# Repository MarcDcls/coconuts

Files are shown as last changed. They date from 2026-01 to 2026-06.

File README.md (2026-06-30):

# CocoNuts Project







The **CocoNuts project** is an open-source humanoid robotics research platform. Its primary design philosophy is the **minimization of leg inertia** by concentrating mass near the root of the limbs, utilizing a combination of timing belts and parallel linkage mechanisms. This repository contains the hardware design of the CocoNuts humanoid platform and the software to operate it with a CANalyst-II interface.

The CAD of the CocoNuts platform is open-source and available under the CERN-OHL-S-2.0 license 
[here](https://cad.onshape.com/documents/326c7618f048bbd5c9f71f42/v/8ddbb93e8d16fabe401f72ed/e/6f8aa33372eceae3daea128b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). The motors used in the robot are RMD-X6 QDD actuators and TD30-40 and TD40-52 harmonic drive actuators.

The software provided is distributed under the Apache-2.0 license and is implemented in Python, which is not adapted for real-time control, but allows to easily set up and test the servomotors and the mechanical design. 

## Mechanical Design

The CocoNuts humanoid platform is designed to minimize leg inertia by relocating the mass of the actuators closer to the body. This is achieved using timing belts at the output of the RMD-X6 motors 
to place the knee and ankle pitch motors near the hip joint:

<p align="center">
  
  
<p\>
  
The transmission of ankle pitch motion is then achieved using a four-bar parallel linkage mechanism:

<p align="center">
  
  
<p\>
  
## Simplified One Leg Benchmark

The prototype of a one leg benchmark of the CocoNuts platform was built to evaluate the performance of the design concept. The CAD of this prototype is available [here](https://cad.onshape.com/documents/326c7618f048bbd5c9f71f42/v/8ddbb93e8d16fabe401f72ed/e/362dba3e9b9b20be3e7fcf95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). Example trajectories were run on the leg to assess its capabilities in three configurations: ankle only actuation, knee only actuation, and both knee and ankle actuation.

<p align="center">
  ankle
  ankle_gif
<p\>

<p align="center">
  knee
  knee_gif
<p\>

<p align="center">
  both
  both_gif
<p\>

The experiments provided critical insights into the platform's design:
- **Actuator Mismatch**: The RMD-X6 motors proved to be oversized for the current scale of the leg. Their high torque capability is offset by their weight, resulting in an unfavorable power-to-weight ratio for this specific frame. This suggests that the design would be more efficient either with a larger structural scale or with lighter, more compact actuators.
- **Mechanical Complexity**: The timing belt and parallel linkage system, while successful in shifting mass towards the body, introduced significant compliance and mechanical play. This complexity led to challenges in achieving precise control.

These findings indicate that a major architectural pivot is required to better align the actuation power with the mechanical structure. As a result, the project is currently on hold and I am maintaining this repository as an open-access technical reference for the robotics community.

# Control Software 

This part of the repository contains the software to operate the RMD-X6 servomotors using a CANalyst-II interface. The software is implemented in Python and allows to set up and test the servomotors.

## Install

To install the repository, you need the uv package manager. 
If you don't have it yet, you can install it by following the instructions [here](https://docs.astral.sh/uv/getting-started/installation/#installation-methods).

Then, clone this repository and run the following command in your terminal:
```
uv sync
```

To use the CANalyst-II device, you need to add a rule to grant USB permissions. To do so, copy the 99-canalyst.rules file provided to 
the `/etc/udev/rules.d/` directory:
```
sudo cp 99-canalyst.rules /etc/udev/rules.d/.
```

## List of motor commands

Several scripts are provided to set up the RMD-X6 servomotors. The available commands are:
- `./set_id.sh <new_id>`: Set the ID of the connected servomotor to `<new_id>`.
- `./ping.sh <ids>`: Ping the list of `<ids>` to check if the servomotors are connected.
- `./set_zeros.sh`: Set the current position of all servomotors as their zero position in their ROM.
- `./stop.sh`: Stop and release all servomotors.
- `./state.sh <ids>`: Display the state (temperature, position, velocity, current, last timestep of reading) of the servomotors in the list of `<ids>`.
- `./set_filter.sh <bool> <ids>`: Set the CAN filter to enable (`<bool>` = 1) or disable (`<bool>` = 0) filtering for the list of `<ids>`. 
- `./set_acceleration.sh <acceleration> <ids>`: Set the maximum acceleration/deceleration for the velocity and position control modes of the servomotors in the list of `<ids>` to `<acceleration>`. Setting `<acceleration>` to 0 disables the acceleration limit and the acceleration follow the default profile of the servomotor.
- `./set_pid.sh <id> <kp> <ki>`: Set the Kp and Ki gains of the servomotor `<id>` to `<kp>` and `<ki>`.
- `./read_rom.sh <ids>`: Display the ROM parameters (acc/dec of the control modes, PID gains) of the servomotors in the list of `<ids>`.

The commands are implemented in the `software/rmd_motor.py` file, which can also be imported as a module in your own Python scripts to write custom motor scripts.

## One leg benchmark

The one leg benchmark can be controlled using the `benchmark.sh` script. The script runs a series of trajectories to test the performance of the leg design. By default, the benchmark runs these trajectories in a meshcat visualizer to verify the motion of the leg before running it physically.

Prior to running the benchmark on the real hardware, make sure to set up the motors by:
- Setting the knee motor ID to 1 and the ankle motor ID to 2 using the `set_id.sh` script.
- Deactivating the CAN filters for both motors using the command `./set_filter.sh 0 1 2`.
- Setting the zero positions of both motors using the command `./set_zeros.sh` while the leg is extended with the foot horizontal. You can verify the zero positions by running the command `./state.sh 1 2` and checking that both motors read a position of 0.
- Setting the acceleration limits of both motors to 0 using the command `./set_acceleration.sh 0 1 2`.

Once the setup is complete, you can run the benchmark using the command:
```
./benchmark.sh <option>
```

where `<option>` can be:
- `--plot`: Plot the motor trajectories instead of running the visualization.
- `--send`: Run the benchmark on the real hardware instead of the visualization.
- `--duration <seconds>`: Set the duration of the trajectory to `<seconds>`.
- `--ankle_only`: Run a sinusoidal trajectory on the ankle motor only.
- `--knee_only`: Run a sinusoidal trajectory on the knee motor only, with the ankle fixed.
- `--zero`: Run a zero position trajectory.

By default the trajectory consists of a sinusoidal motion of both the knee and ankle motors with a duration of 4 * pi seconds.

# Citation

To cite this repository in your publications:
```bibtex
@software{mduclusaud-coconuts,
    author = {Duclusaud, Marc},
    doi = {10.5281/zenodo.18470949},
    month = feb,
    title = {{CocoNuts: An open-source humanoid robotics platform minimizing leg inertia}},
    url = {https://github.com/MarcDcls/coconuts},
    howpublished = "\url{https://github.com/MarcDcls/coconuts}",
    version = {1.0.0},
    year = {2026}
}
```

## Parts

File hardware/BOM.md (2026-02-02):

# Bill of Materials

- 4x RMD X6 1:6 
- 4x TD 30-40
- 4x TD 40-52

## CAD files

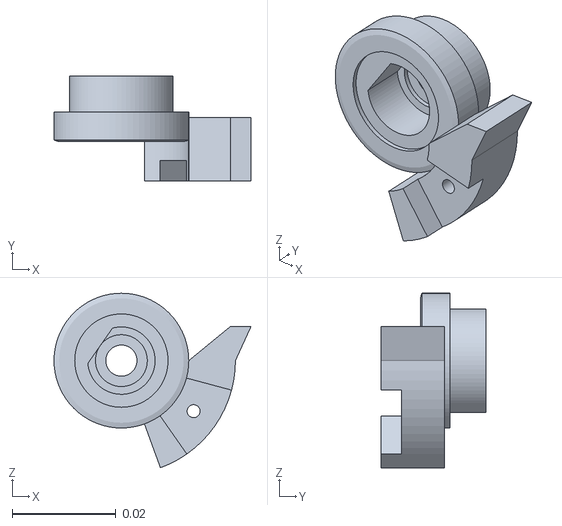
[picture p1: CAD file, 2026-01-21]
hardware/benchmark/assets/benchmark_outer_knee.stl
0.038 x 0.0203 x 0.0337

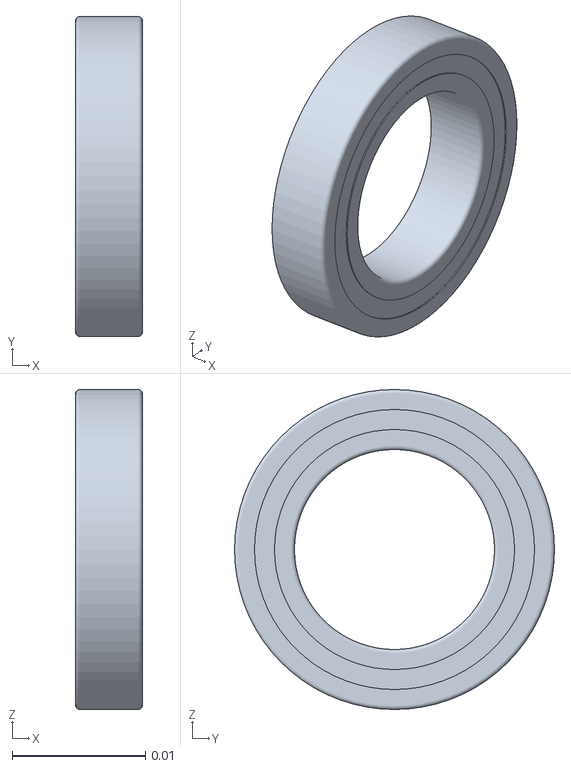
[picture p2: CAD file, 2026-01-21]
hardware/benchmark/assets/bearing_6802_2rs.stl
0.005 x 0.024 x 0.024

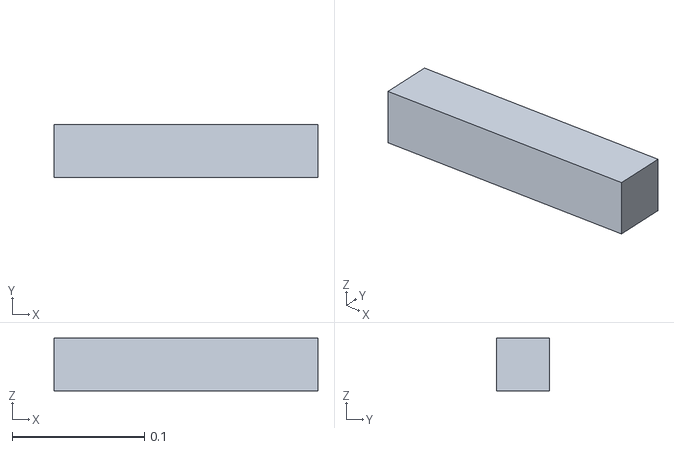
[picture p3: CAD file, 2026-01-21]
hardware/benchmark/assets/aluminum_profile.stl
0.2 x 0.04 x 0.04

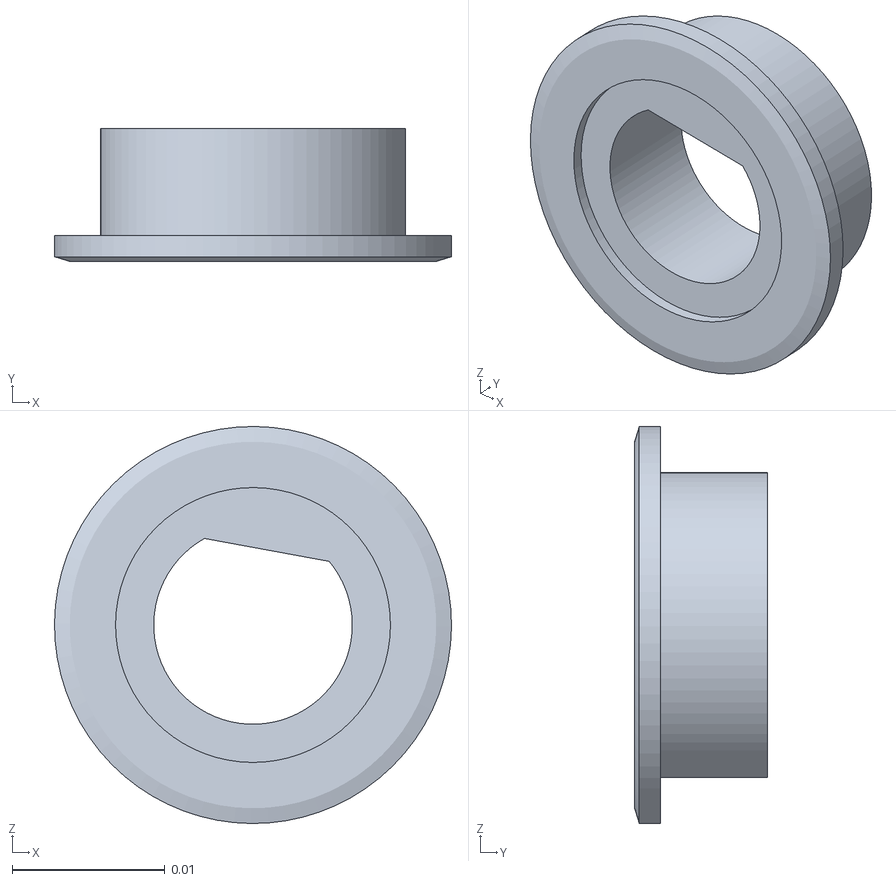
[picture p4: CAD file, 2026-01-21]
hardware/benchmark/assets/outer_crank.stl
0.026 x 0.0087 x 0.026

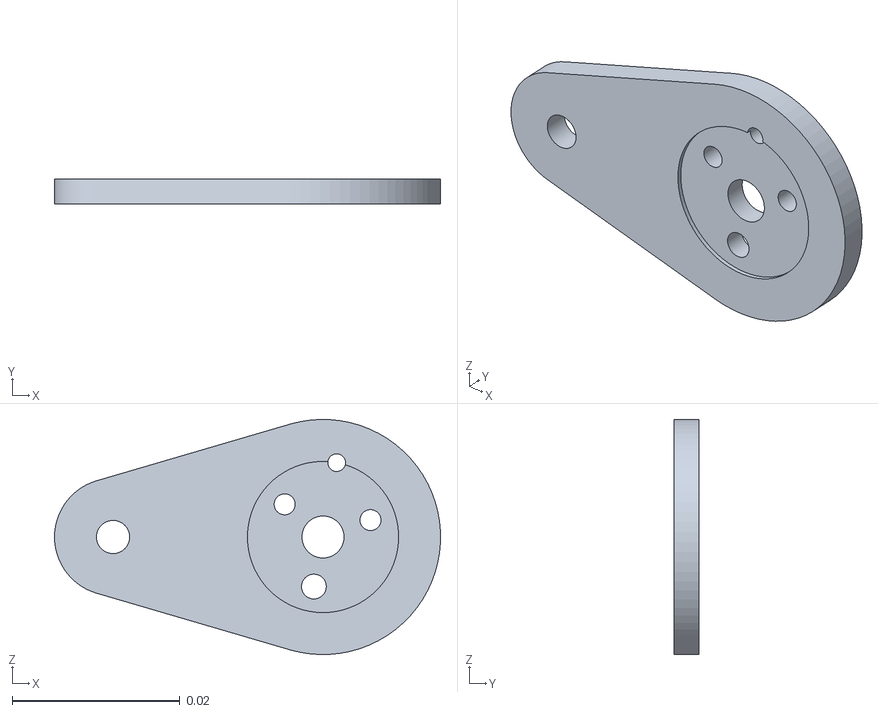
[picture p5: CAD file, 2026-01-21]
hardware/benchmark/assets/outer_crank_alu_mirror.stl
0.046 x 0.003 x 0.028

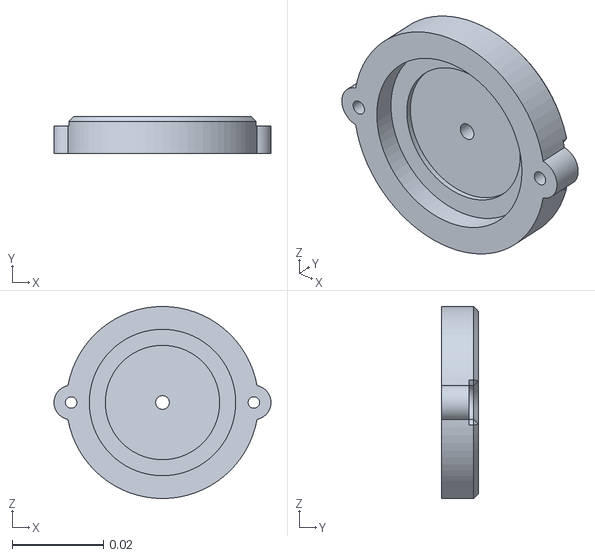
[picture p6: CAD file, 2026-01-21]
hardware/benchmark/assets/bearing_cover_1.stl
0.0474 x 0.008 x 0.042

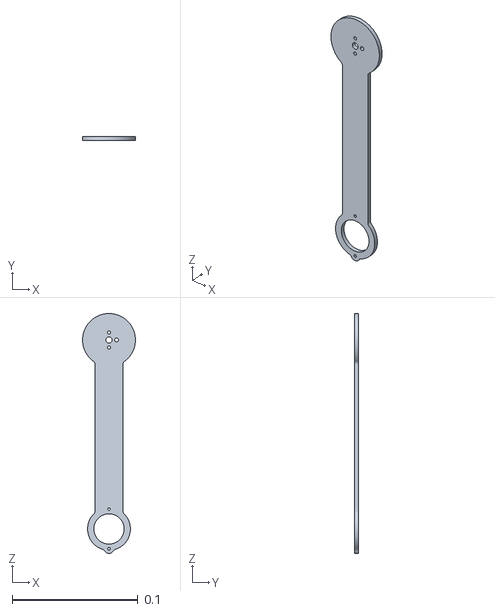
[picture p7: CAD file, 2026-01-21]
hardware/benchmark/assets/inner_tibia.stl
0.042 x 0.003 x 0.19

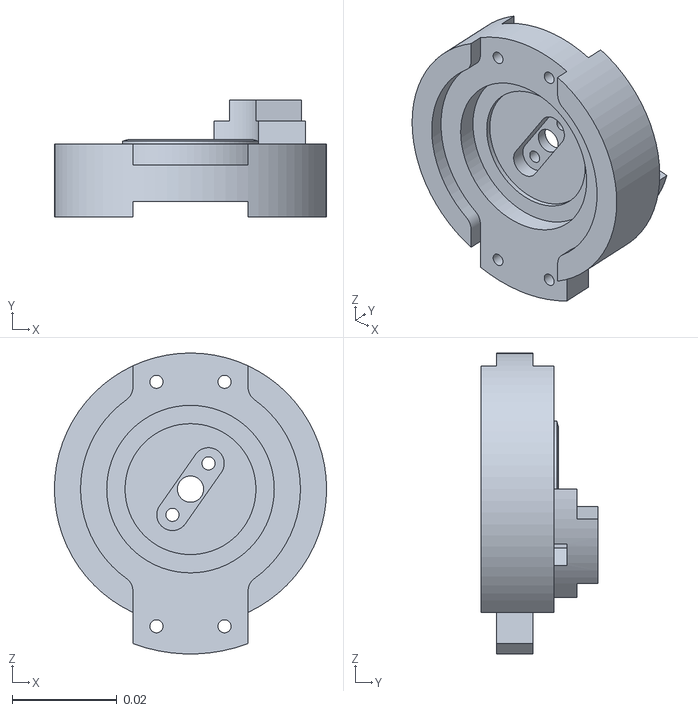
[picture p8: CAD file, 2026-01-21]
hardware/benchmark/assets/outer_knee_2.stl
0.052 x 0.0224 x 0.0575

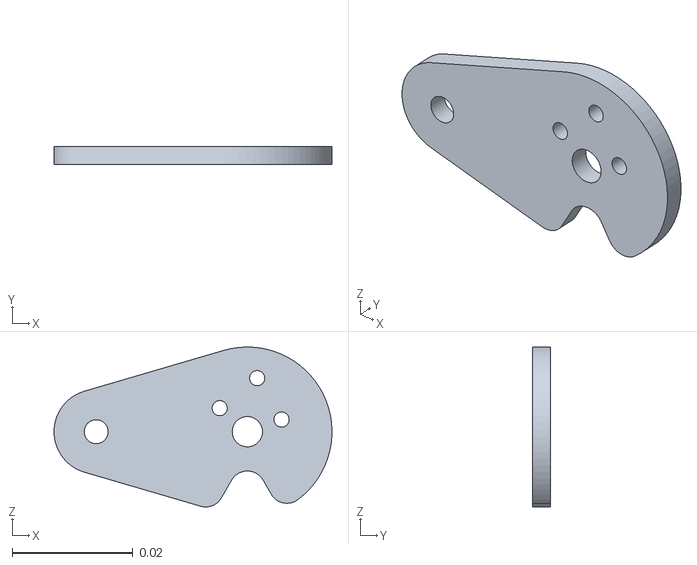
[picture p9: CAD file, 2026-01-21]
hardware/benchmark/assets/inner_crank_alu.stl
0.046 x 0.003 x 0.0264

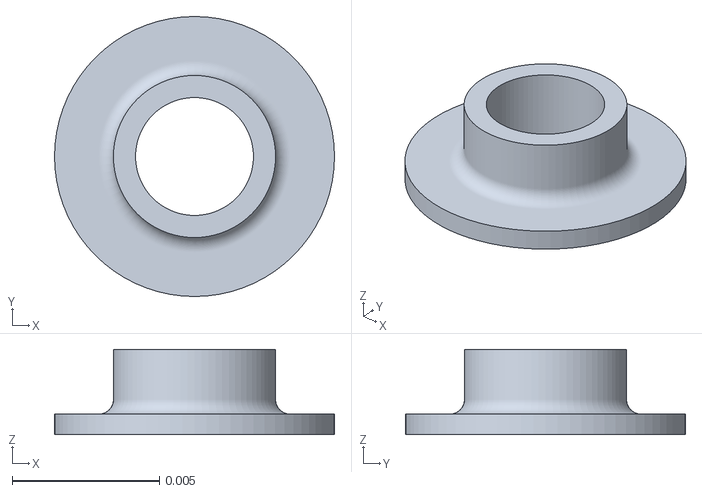
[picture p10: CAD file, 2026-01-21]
hardware/benchmark/assets/p210fm_plain_bearing.stl
0.0095 x 0.0095 x 0.0029

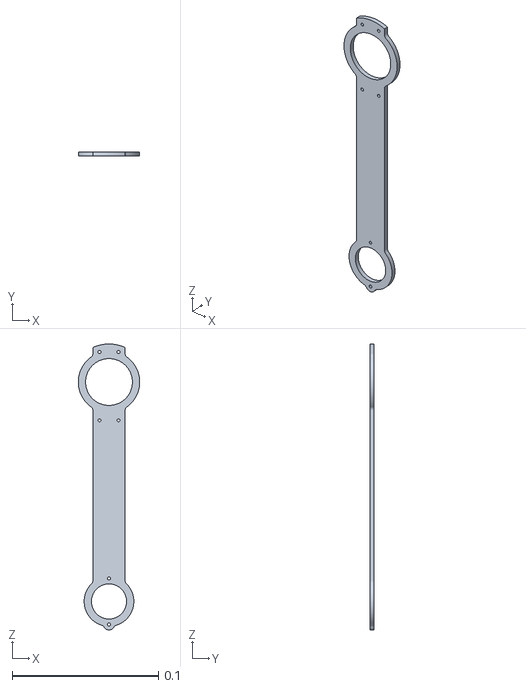
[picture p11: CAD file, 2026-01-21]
hardware/benchmark/assets/outer_tibia.stl
0.042 x 0.003 x 0.195

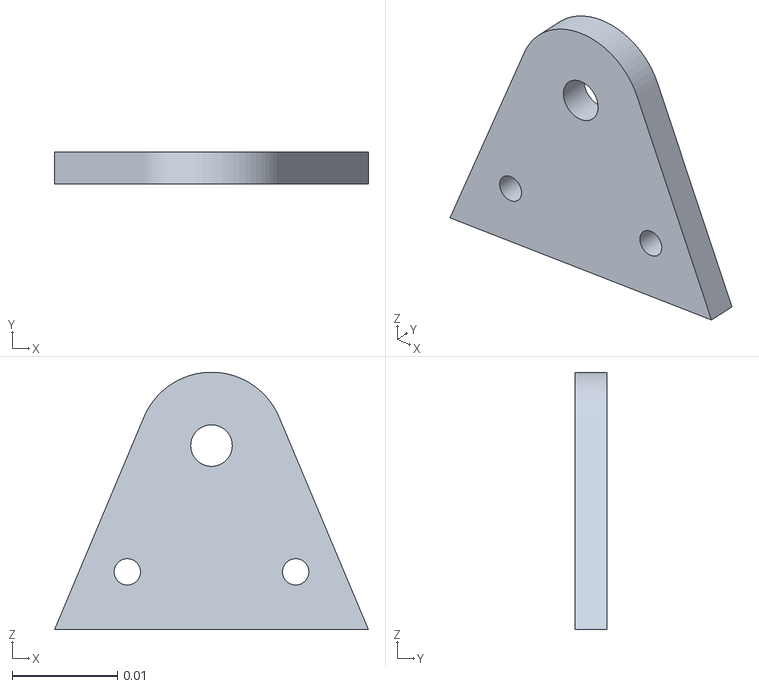
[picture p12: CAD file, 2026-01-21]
hardware/benchmark/assets/ankle_alu.stl
0.0298 x 0.003 x 0.0245

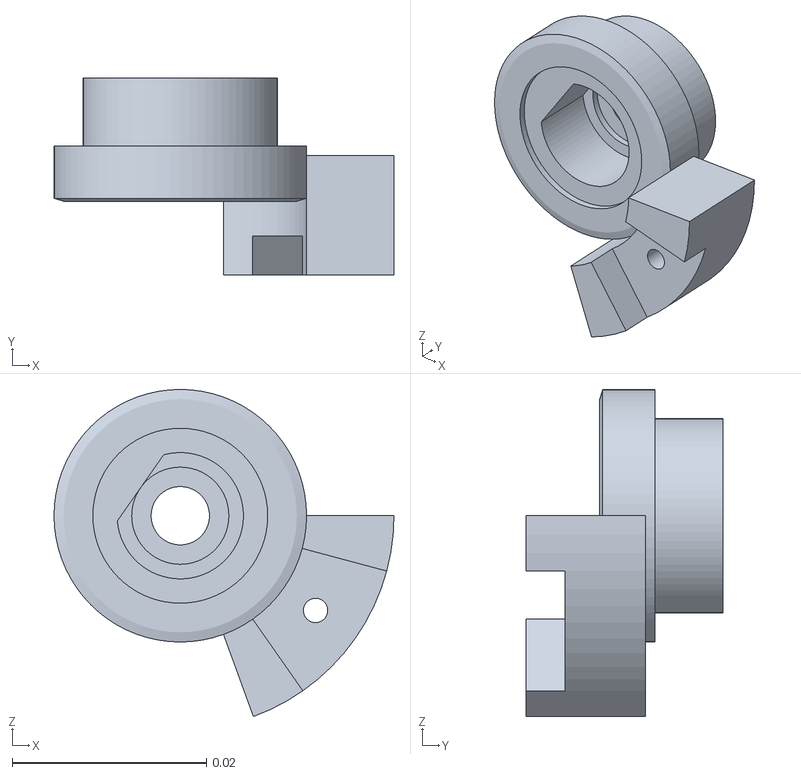
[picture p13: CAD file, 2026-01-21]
hardware/benchmark/assets/outer_knee_1.stl
0.035 x 0.0203 x 0.0337

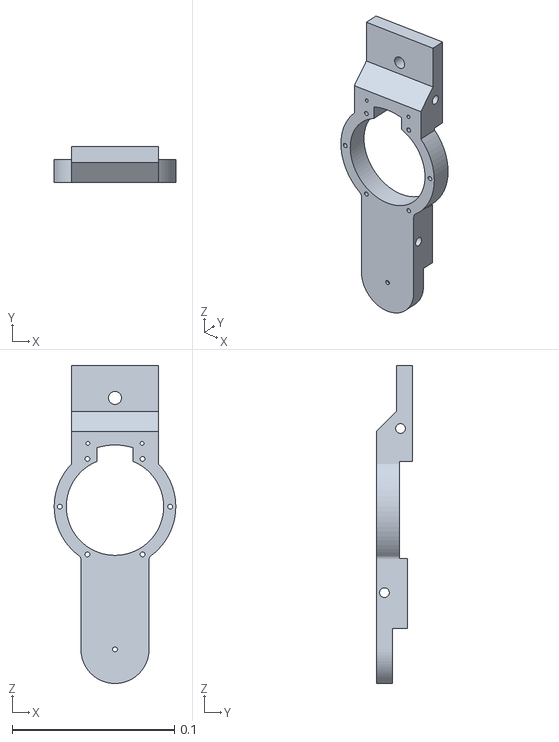
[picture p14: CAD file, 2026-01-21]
hardware/benchmark/assets/benchmark_inner_femur.stl
0.075 x 0.0224 x 0.196

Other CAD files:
hardware/benchmark/assets/benchmark_back_cover.stl
hardware/benchmark/assets/middle_crank.stl
hardware/benchmark/assets/benchmark_outer_hip.stl
hardware/benchmark/assets/inner_crank_mirror.stl
hardware/benchmark/assets/ankle_bearing_cover.stl
hardware/benchmark/assets/ankle_mirror.stl
hardware/benchmark/assets/ankle_shaft.stl
hardware/benchmark/assets/bearing_6804_2rs.stl
hardware/benchmark/assets/benchmark_foot.stl
hardware/benchmark/assets/benchmark_front_cover.stl
hardware/benchmark/assets/benchmark_outer_femur.stl
hardware/benchmark/assets/din_6325_3mm__configuration__12.stl
hardware/benchmark/assets/din_6325_3mm__configuration__6.stl
hardware/benchmark/assets/din_6325_4mm__configuration__14.stl
hardware/benchmark/assets/din_6325_4mm__configuration__20.stl
hardware/benchmark/assets/inner_knee.stl
hardware/benchmark/assets/knee_pulley.stl
hardware/benchmark/assets/knee_pulley_2.stl
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

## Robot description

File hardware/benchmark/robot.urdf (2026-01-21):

<?xml version="1.0" ?>
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
<robot name="benchmark">
  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
  <link name="aluminum_profile">
    <inertial>
      <origin xyz="0 0 0" rpy="0 0 0"/>
      <mass value="0"/>
      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
    </inertial>
    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
  </link>
  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
  <link name="motor_pulley">
    <inertial>
      <origin xyz="-6.05622e-16 4.59528e-05 -0.010399" rpy="0 0 0"/>
      <mass value="0.0695532"/>
      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
    </inertial>
    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
  </link>
  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
  <joint name="knee_motor" type="revolute">
    <origin xyz="-0.000132957 0 0.42" rpy="1.5708 5.23711e-65 3.14159"/>
    <parent link="aluminum_profile"/>
    <child link="motor_pulley"/>
    <axis xyz="0 0 1"/>
    <limit effort="10" velocity="10" lower="-3.141592653589793" upper="3.141592653589793"/>
  </joint>
  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
  <link name="inner_knee">
    <inertial>
      <origin xyz="0.000201294 -0.0560108 -0.0375295" rpy="0 0 0"/>
      <mass value="0.139137"/>
      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
    </inertial>
    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
  </link>
  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
  <link name="left_crank">
    <inertial>
      <origin xyz="-0.000293429 0.00222468 -0.020286" rpy="0 0 0"/>
      <mass value="0.055694"/>
      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
    </inertial>
    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
  </link>
  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
  <link name="ankle_shaft">
    <inertial>
      <origin xyz="-0.075 0.0250001 -0.0034" rpy="0 0 0"/>
      <mass value="0.0280654"/>
      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
    </inertial>
    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
  </link>
  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
  <link name="closing_crank">
    <origin xyz="0 0 0" rpy="0 -0 0"/>
    <inertial>
      <origin xyz="0 0 0" rpy="0 0 0"/>
      <mass value="1e-9"/>
      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
    </inertial>
  </link>
  <joint name="closing_crank_frame" type="fixed">
    <origin xyz="-0.15 0.05 -0.0068" rpy="1.5708 -6.11275e-15 -1.50324e-15"/>
    <parent link="ankle_shaft"/>
    <child link="closing_crank"/>
    <axis xyz="0 0 0"/>
  </joint>
  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
  <joint name="upper_crank" type="revolute">
    <origin xyz="-4.14113e-14 0.025 -0.029" rpy="3.14159 -1.67015e-15 2.49809"/>
    <parent link="left_crank"/>
    <child link="ankle_shaft"/>
    <axis xyz="0 0 1"/>
    <limit effort="10" velocity="10" lower="-3.141592653589793" upper="3.141592653589793"/>
  </joint>
  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
  <joint name="ankle_passive" type="revolute">
    <origin xyz="0 0 -0.005" rpy="1.65388e-31 -2.80452e-29 -1.5708"/>
    <parent link="inner_knee"/>
    <child link="left_crank"/>
    <axis xyz="0 0 1"/>
    <limit effort="10" velocity="10" lower="-1.5708" upper="1.22173"/>
  </joint>
  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
  <link name="benchmark_foot">
    <inertial>
      <origin xyz="0.00774961 -0.0296086 -0.0198932" rpy="0 0 0"/>
      <mass value="0.0537006"/>
      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
    </inertial>
    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
  </link>
  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
  <link name="closing_foot">
    <origin xyz="0 0 0" rpy="0 -0 0"/>
    <inertial>
      <origin xyz="0 0 0" rpy="0 0 0"/>
      <mass value="1e-9"/>
      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
    </inertial>
  </link>
  <joint name="closing_foot_frame" type="fixed">
    <origin xyz="0.025 -1.11022e-16 -0.0232" rpy="1.5708 -1.80862e-16 -3.14159"/>
    <parent link="benchmark_foot"/>
    <child link="closing_foot"/>
    <axis xyz="0 0 0"/>
  </joint>
  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
  <link name="foot">
    <origin xyz="0 0 0" rpy="0 -0 0"/>
    <inertial>
      <origin xyz="0 0 0" rpy="0 0 0"/>
      <mass value="1e-9"/>
      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
    </inertial>
  </link>
  <joint name="foot_frame" type="fixed">
    <origin xyz="-0.00573895 -0.0515 -0.0197" rpy="1.5708 -1.89761e-17 -3.14159"/>
    <parent link="benchmark_foot"/>
    <child link="foot"/>
    <axis xyz="0 0 0"/>
  </joint>
  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
  <joint name="ankle_joint" type="revolute">
    <origin xyz="5.42101e-20 -0.15 -0.0503" rpy="3.14159 2.1445e-17 -3.14159"/>
    <parent link="inner_knee"/>
    <child link="benchmark_foot"/>
    <axis xyz="0 0 1"/>
    <limit effort="10" velocity="10" lower="-1.22173" upper="1.5708"/>
  </joint>
  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
  <joint name="knee_joint" type="revolute">
    <origin xyz="-0.000132957 -0.0835 0.269" rpy="1.5708 -0 1.64748e-23"/>
    <parent link="aluminum_profile"/>
    <child link="inner_knee"/>
    <axis xyz="0 0 1"/>
    <limit effort="10" velocity="10" lower="-2.0944" upper="0"/>
  </joint>
  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
  <link name="motor_pulley_2">
    <inertial>
      <origin xyz="-6.05768e-16 4.59528e-05 -0.010399" rpy="0 0 0"/>
      <mass value="0.0695532"/>
      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
    </inertial>
    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
  </link>
  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
  <joint name="ankle_motor" type="revolute">
    <origin xyz="-0.000132957 -0.0533001 0.357" rpy="1.5708 -1.5708 0"/>
    <parent link="aluminum_profile"/>
    <child link="motor_pulley_2"/>
    <axis xyz="0 0 1"/>
    <limit effort="10" velocity="10" lower="-3.141592653589793" upper="3.141592653589793"/>
  </joint>
</robot>

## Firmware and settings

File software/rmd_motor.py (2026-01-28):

# Copyright 2026 Marc Duclusaud

# Licensed under the Apache License, Version 2.0 (the "License");
# you may not use this file except in compliance with the License.
# You may obtain a copy of the License at:

#     http://www.apache.org/licenses/LICENSE-2.0

import can
import time

BITRATE = 1000000 # 1 Mbps


class RMDMotor:
    """
    Python interface for MyActuator RMD-X/L series motors over CAN bus.
    """
    def __init__(self, bus, id: int=1):
        self.bus = bus
        self.motor_id = id
        self.status = {
            "temp": 0,       # °C
            "current": 0.0,  # A
            "speed": 0,      # deg/s
            "position": 0,   # deg
            "last_update": 0 # s
        }

    def _send(self, data):
        """
        Sends a 8-byte CAN frame without waiting for a response.
        """
        msg = can.Message(
            arbitration_id=self.motor_id + 0x140,
            data=data,
            is_extended_id=False
        )
        try:
            self.bus.send(msg)
        except can.CanError as e:
            print(f"CAN Error: {e}")

    def update_status(self, data):
        """
        Updates the motor status based on received CAN data.
        """

        # Status update
        if data[0] in [0x9C, 0xA4]:
            self.status.update({
                "temp": data[1],
                "current": int.from_bytes(data[2:4], byteorder='little', signed=True) * 100, # Unit to verify
                "speed": int.from_bytes(data[4:6], byteorder='little', signed=True), 
                "position": int.from_bytes(data[6:8], byteorder='little', signed=True), 
                "last_update": time.perf_counter()
            })
        
        # PID print
        elif data[0] in [0x30, 0x31, 0x32]:
            print(f"Motor ID {self.motor_id} PID parameters:")
            print(f"  Current Kp: {data[2]}")
            print(f"  Current Ki: {data[3]}")
            print(f"  Velocity Kp: {data[4]}")
            print(f"  Velocity Ki: {data[5]}")
            print(f"  Position Kp: {data[6]}")
            print(f"  Position Ki: {data[7]}", flush=True)

        # Ping print
        elif data[0] == 0x01:
            print(f"Motor ID {self.motor_id} responded to ping.", flush=True)

        # Acceleration print
        elif data[0] == 0x42:
            if data[1] == 0x00:
                print(f"Motor ID {self.motor_id} position planning acceleration: {int.from_bytes(data[4:8], byteorder='little', signed=False)}", flush=True)
            elif data[1] == 0x01:
                print(f"Motor ID {self.motor_id} position planning deceleration: {int.from_bytes(data[4:8], byteorder='little', signed=False)}", flush=True)
            elif data[1] == 0x02:
                print(f"Motor ID {self.motor_id} velocity planning acceleration: {int.from_bytes(data[4:8], byteorder='little', signed=False)}", flush=True)
            elif data[1] == 0x03:
                print(f"Motor ID {self.motor_id} velocity planning deceleration: {int.from_bytes(data[4:8], byteorder='little', signed=False)}", flush=True)
            
    # --- UTILITY COMMANDS ---
    
    def ping(self):
        """Sends a ping command to check if the motor is responsive."""
        self._send([0x01, 0x00, 0x00, 0x00, 0x00, 0x00, 0x00, 0x00])

    def read_status(self):
        """Reads motor temperature, voltage, and error flags (Command 0x9C)."""
        self._send([0x9C, 0x00, 0x00, 0x00, 0x00, 0x00, 0x00, 0x00])
    
    def read_acceleration(self, pos_acc: bool=True, pos_dec: bool=True, vel_acc: bool=True, vel_dec: bool=True):
        """Reads the acceleration setting from the motor (Command 0x42)."""
        if pos_acc:
            self._send([0x42, 0x00, 0x00, 0x00, 0x00, 0x00, 0x00, 0x00])
            time.sleep(0.1)
        if pos_dec:
            self._send([0x42, 0x01, 0x00, 0x00, 0x00, 0x00, 0x00, 0x00])
            time.sleep(0.1)
        if vel_acc:
            self._send([0x42, 0x02, 0x00, 0x00, 0x00, 0x00, 0x00, 0x00])
            time.sleep(0.1)
        if vel_dec:
            self._send([0x42, 0x03, 0x00, 0x00, 0x00, 0x00, 0x00, 0x00])
            time.sleep(0.1)
        
    def read_pid(self):
        """Reads the current proportional gain Kp from the motor (Command 0x30)."""
        self._send([0x30, 0x00, 0x00, 0x00, 0x00, 0x00, 0x00, 0x00])

    # --- CONFIGURATION COMMANDS ---

    def set_zero(self):
        """Sets the current multi-turn position as the encoder zero position in the ROM (Command 0x64)."""
        self._send([0x64, 0x00, 0x00, 0x00, 0x00, 0x00, 0x00, 0x00])

    def restart(self):
        """Restarts the motor system (Command 0x76)."""
        self._send([0x76, 0x00, 0x00, 0x00, 0x00, 0x00, 0x00, 0x00])

    def active_reply(self, cmd: int, enable: bool, interval_10ms: int=0):
        """Enables or disables active reply mode (Command 0xB6)."""
        flag = 0x01 if enable else 0x00
        interval = interval_10ms.to_bytes(4, byteorder='little', signed=False)
        self._send([0xB6, cmd, flag, interval[0], interval[1], 0x00, 0x00, 0x00])

    def filter_mode(self, enable: bool):
        """Enables or disables motor broadcast mode."""
        flag = 0x01 if enable else 0x00
        self._send([0x20, 0x02, 0x00, 0x00, flag, 0x00, 0x00, 0x00])

    def set_id(self, new_id: int):
        """Sets a new motor ID (Command 0x79)."""
        self._send([0x79, 0x00, 0x00, 0x00, 0x00, 0x00, 0x00, new_id])
    
    def write_acceleration(self, value: int, pos_acc: bool=True, pos_dec: bool=True, vel_acc: bool=True, vel_dec: bool=True):
        """Writes the acceleration setting to the motor RAM and ROM (Command 0x43)."""
        value_bytes = value.to_bytes(4, byteorder='little', signed=False)
        if pos_acc:
            self._send([0x43, 0x00, 0x00, 0x00] + list(value_bytes))
            time.sleep(0.1)
        if pos_dec:
            self._send([0x43, 0x01, 0x00, 0x00] + list(value_bytes))
            time.sleep(0.1)
        if vel_acc:
            self._send([0x43, 0x02, 0x00, 0x00] + list(value_bytes))
            time.sleep(0.1)
        if vel_dec:
            self._send([0x43, 0x03, 0x00, 0x00] + list(value_bytes))
            time.sleep(0.1)
            
    def write_pid(self, cur_kp: int=0, cur_ki: int=0, vel_kp: int=0, vel_ki: int=0, pos_kp: int=0, pos_ki: int=0, to_rom: bool=True):
        """Writes position proportional gain Kp to non-volatile ROM (Command 0x32) or volatile RAM (Command 0x31)."""
        cmd = 0x32 if to_rom else 0x31
        self._send([cmd, 0x00, cur_kp, cur_ki, vel_kp, vel_ki, pos_kp, pos_ki])
        
    # --- CONTROL COMMANDS ---

    def stop_motor(self):
        """Turns off the motor and clears any running state (Command 0x80)."""
        self._send([0x80, 0x00, 0x00, 0x00, 0x00, 0x00, 0x00, 0x00])

    def brake_motor(self):
        """Stops the motor and holds position (Command 0x81)."""
        self._send([0x81, 0x00, 0x00, 0x00, 0x00, 0x00, 0x00, 0x00])
    
    def set_position(self, angle_deg: float, max_speed_dps: int=3600):
        """Multi-turn absolute position control (Command 0xA4).
        Value: angle in degrees. Protocol uses 0.01 deg/LSB.
        """
        angle_val = int(angle_deg * 100)
        angle_bytes = angle_val.to_bytes(4, byteorder='little', signed=True)
        max_speed_bytes = int(max_speed_dps).to_bytes(2, byteorder='little', signed=False)
        data = [0xA4, 0x00] + list(max_speed_bytes) + list(angle_bytes)
        self._send(data)

    # --- STATUS GETTERS ---

    def get_position(self):
        """Returns the last known position in degrees."""
        return self.status["position"]
    
    def get_velocity(self):
        """Returns the last known velocity in degrees per second."""
        return self.status["speed"]
    
    def get_current(self):
        """Returns the last known current in Amperes."""
        return self.status["current"]
    
    def get_temperature(self):
        """Returns the last known temperature in degrees Celsius."""
        return self.status["temp"]
    
    def get_last_update_time(self):
        """Returns the timestamp of the last status update."""
        return self.status["last_update"]


class RMDMotorBroadcast(RMDMotor):
    """
    Subclass for broadcasting commands to all motors on the CAN bus.
    """
    def __init__(self, bus):
        super().__init__(bus, id=(0x280 - 0x140))  # Broadcast ID is 0x280


class RMDListener(can.Listener):
    """
    Asynchronous listener that intercepts CAN messages and updates 
    the corresponding RMDMotor instances.
    """
    def __init__(self, motors_dict):
        """
        """
        self.motors = motors_dict 

    def on_message_received(self, msg):
        if msg.arbitration_id - 0x240 in self.motors:
            id = msg.arbitration_id - 0x240
            self.motors[id].update_status(msg.data)


if __name__ == "__main__":
    import can.interfaces.canalystii as canalystii
    import time
    import sys

    if len(sys.argv) <= 1:
        print("Usage: python rmd_motor.py [IDS]")
        print("Example: python rmd_motor.py 1 2 3")
        sys.exit(1) 

    ids = [int(arg) for arg in sys.argv[1:]]

    with canalystii.CANalystIIBus(channel=0, bitrate=BITRATE, receive_own_messages=False) as bus:
        motors = {}
        for id in ids:
            motors[id] = RMDMotor(bus, id)

        listener = RMDListener(motors)
        with can.Notifier(bus, [listener]):
            while True:
                step_start = time.time()

                for id, motor in motors.items():
                    motor.read_status()
                    print(f"Motor ID {id} status: {motor.status}")
                
                while time.time() - step_start < 0.1:
                    time.sleep(1e-4)

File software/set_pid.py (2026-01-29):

# Copyright 2026 Marc Duclusaud

# Licensed under the Apache License, Version 2.0 (the "License");
# you may not use this file except in compliance with the License.
# You may obtain a copy of the License at:

#     http://www.apache.org/licenses/LICENSE-2.0

import can
import can.interfaces.canalystii as canalystii
from rmd_motor import BITRATE, RMDMotor, RMDListener
import time
import sys

if len(sys.argv) != 4:
    print("Usage: python set_filter.py [ID] [Kp] [Ki]")
    print("Example: python set_filter.py 1 100 5")
    sys.exit(1)

motor_id = int(sys.argv[1])
Kp = float(sys.argv[2])
Ki = float(sys.argv[3])

# Default current and velocity PI values
cur_kp = 100
cur_ki = 100
vel_kp = 100
vel_ki = 5

with canalystii.CANalystIIBus(channel=0, bitrate=BITRATE, receive_own_messages=False) as bus:
    motors = {motor_id: RMDMotor(bus, motor_id)}

    listener = RMDListener(motors)
    with can.Notifier(bus, [listener]):
        for id, motor in motors.items():
            motor.write_pid(cur_kp, cur_ki, vel_kp, vel_ki, Kp, Ki, to_rom=True)
            time.sleep(0.3)

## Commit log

2026-01-15 Update README with USB device configuration steps
    Added instructions for configuring USB device rules and loading modules.
2026-01-21 Adding benchmark model
    [aluminum_profile.stl, ankle_alu.stl, ankle_bearing_cover.stl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]
2026-01-21 Benchmark control
    [benchmark_outer_knee.stl, robot.urdf]
2026-01-21 RMD motor class
2026-01-22 Framerate improvement
2026-01-23 Benchmark functional, investigating PID problems
    [benchmark.py, move.py, ping.py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]
2026-01-30 PID script
2026-01-30 Add images to one leg benchmark section
    Added images to the one leg benchmark section for better visualization.
2026-01-30 Add items to Bill of Materials

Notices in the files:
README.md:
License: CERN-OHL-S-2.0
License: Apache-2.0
